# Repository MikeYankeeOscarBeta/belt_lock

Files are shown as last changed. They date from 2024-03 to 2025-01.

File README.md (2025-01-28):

# belt_lock
by [MikeYankeeOscarBeta](https://github.com/MikeYankeeOscarBeta/) (VoronDesign Discord: #MikeyMike V2.5796, Voron Toolchangers Discord: MikeyMike - Github: [MikeYankeeOscarBeta](https://github.com/MikeYankeeOscarBeta/StealthChanger))

## Description
A solution for mounting 9mm and 6mm 2mgt/2gt GT2/GT3 belts to mgn12 carriage with M2-SHCS or 2mm pin. Designed to handle high belt tensions.
Versions for both inverted and normal belts.

## Features
- Belt Pin
- Does not clamp the belt against the carriage, carriage-wipers or anything other than itself
- For monolith (inverted belts) it will not change the belt path (keeps the belt path perfectly straight)
- For normal belt direction there will be a ~0.8mm y offset
- Keeps within the confines of the carriage (unless using the external clamps)
- builds just 6mm out in y
- Tested with 15kg static load per belt

## BOM
| Part | Amount | Description |
|---|---|---|
| M2x25mm SHCS or 2x25mm PIN  | 4 |  Pin leaves more material, hence stronger. |
| | |  M2 SHCS for ease of use |
| | |  (only 2 screws if using single pin and clamp version (shuttle_clamper_body_v75) |

## Print Instructions
- Print it upright, the strength comes from the layer direction. printing it in the incorrect orientation will result in a weaker part.  
- Use support (make sure your supports are tuned to the point where you're able to remove them carefully without breaking the part).  
- 40%+ infill  
- 4 perimitters  
- 4 top and bottom layers  
- 0.2mm layer height  (or smaller)
- 0.4mm nozzle (or smaller)
- enable filling gaps

## Part Instructions
### shuttle_clamper_body_v101_inverted_belt_gt2_epdm
main body, for no loss in x.
For inverted belts in EPDM (LL-GT2 E) and GT3. will be too loose for normal GT2 (rubber) belts.
Should work with GT2 RF (rubber/normal) belts as well, but will slip sooner (<15kg)

### shuttle_clamper_body_v96_*
main body, for no loss in x.
For inverted belts gt2 rubber belts (LL-2GT RF). Too tight for GT2 EPDM or GT3.

### shuttle_clamper_body_v96_normal_belt
For normal (non-inverted) GT2-R (rubber) belts.

### shuttle_clamper_body_v75
Single pin, no teardrop lock. For both normal and inverted belts. GT2 rubber and epdm, and GT3.
Requires use with a clamp like m2_belt_clamp or m3_BeefyBeltClamp.

### m2_belt_clamp
small footprint belt clamp using m2 screws and heatset nuts.

### m3_BeefyBeltClamp
Beefy clamp using m3 screws and hexnuts.

### BOM - m2_belt_clamp
| Part | Amount | Description |
|---|---|---|
| m2x4x3.5 Heatset Nut | 6 |  4mm deep, m2 threads, 3.5mm outer diameter |
| m2x10mm SHCS Screw | 6 |  m2x12 SHCS also works ok |

### BOM - m3_BeefyBeltClamp
| Part | Amount | Description |
|---|---|---|
| m3 hexnut | 6 | |
| m3x8mm SHCS Screw | 6 | m3x12 SHCS also works |

## Support
Raise issues via github or contact via discord.
Voron Toolchangers Discord "Belt Lock" thread: https://discord.com/channels/1119433664799965186/1218280403870289990

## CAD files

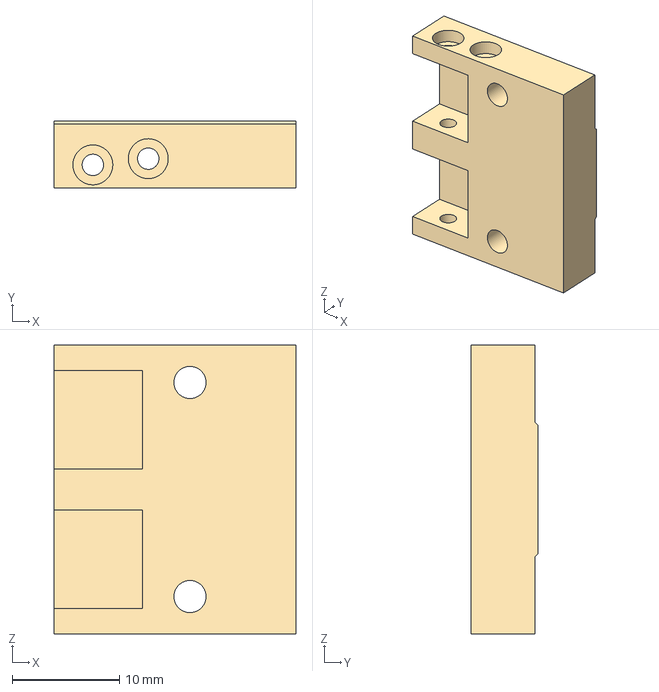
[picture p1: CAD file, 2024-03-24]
CAD/shuttlething_v0.3_v101_inverted_belt_gt2_epdm.step
22.6 x 6.30 x 27.0 mm

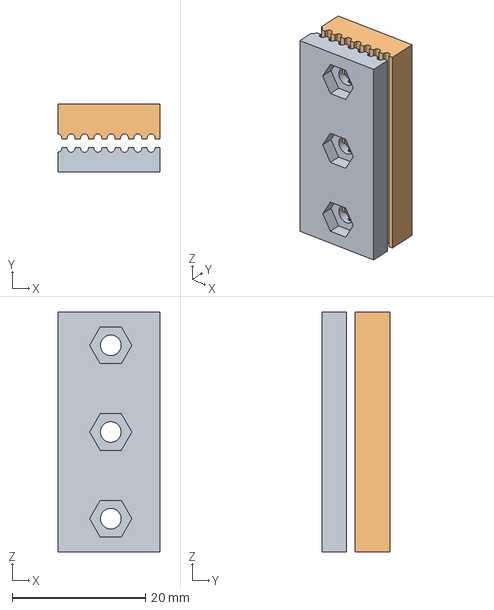
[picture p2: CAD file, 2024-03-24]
CAD/m3_BeefyBeltClamp_v2.step
15.3 x 10.2 x 36.0 mm

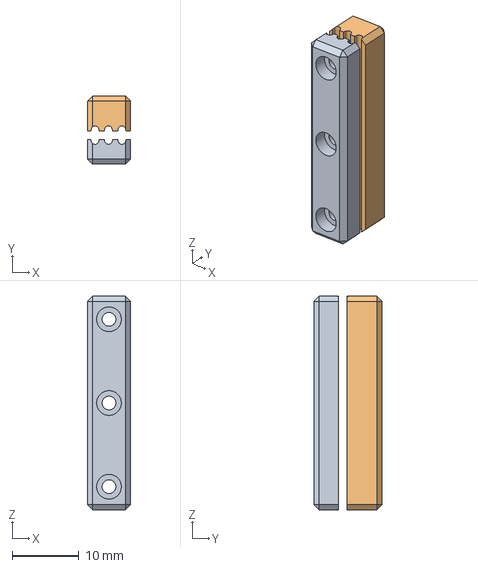
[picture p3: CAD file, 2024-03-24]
CAD/m2_belt_clamp_v70.step
6.50 x 10.2 x 32.0 mm
m2_belt_clamp_a
m2_belt_clamp_b

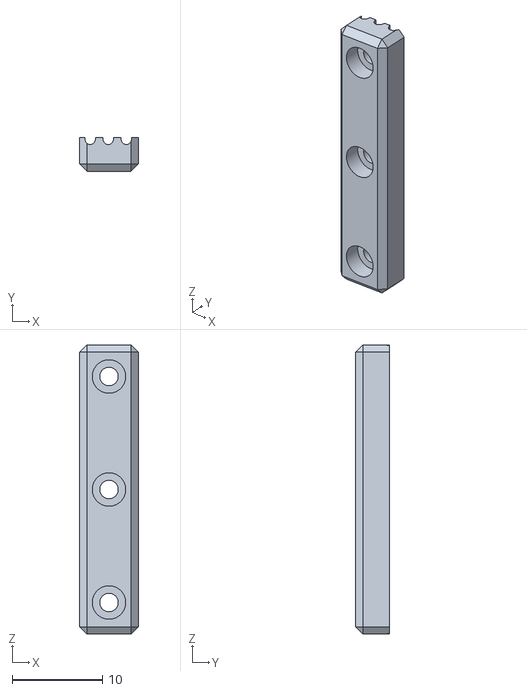
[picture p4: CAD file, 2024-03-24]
STL/m2_belt_clamp_a_v70.stl
6.50 x 3.71 x 32.0

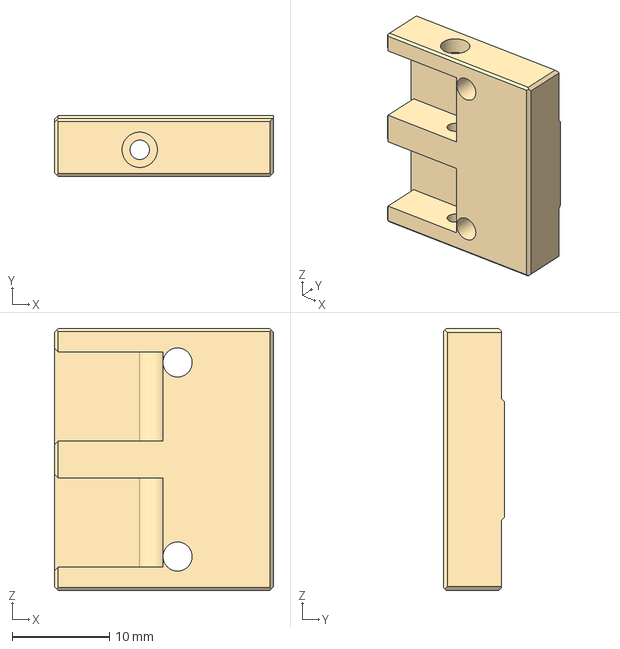
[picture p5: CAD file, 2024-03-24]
CAD/shuttle_clamper_body_v75.step
22.6 x 6.30 x 27.0 mm

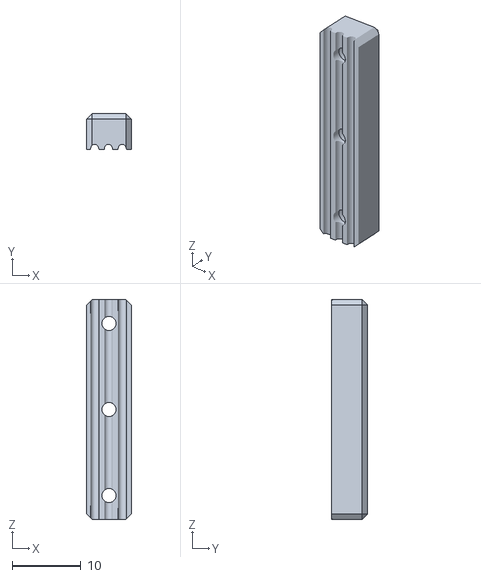
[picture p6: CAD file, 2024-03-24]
STL/m2_belt_clamp_b_v70.stl
6.50 x 5.24 x 32.0

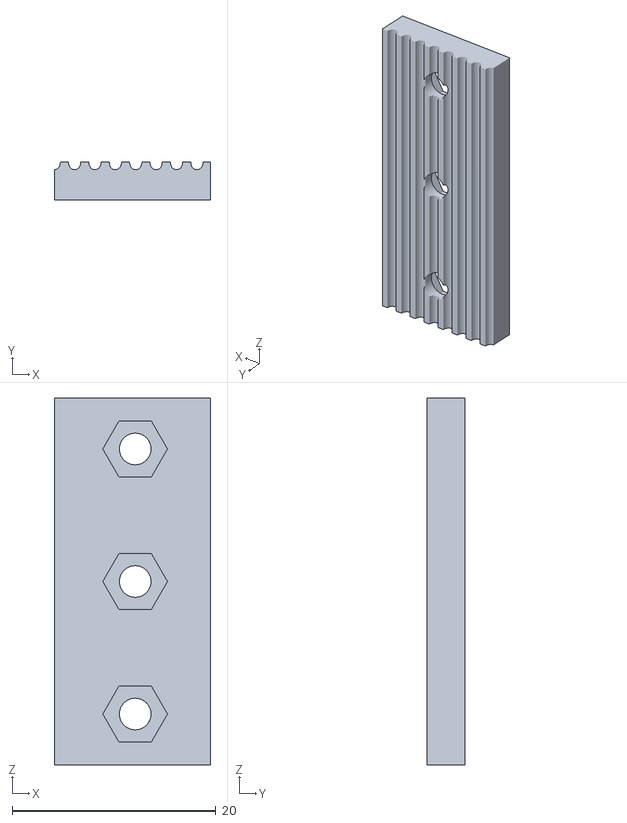
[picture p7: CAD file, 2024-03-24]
STL/m3_BeefyBeltClamp_a_v2.stl
15.3 x 3.71 x 36.0

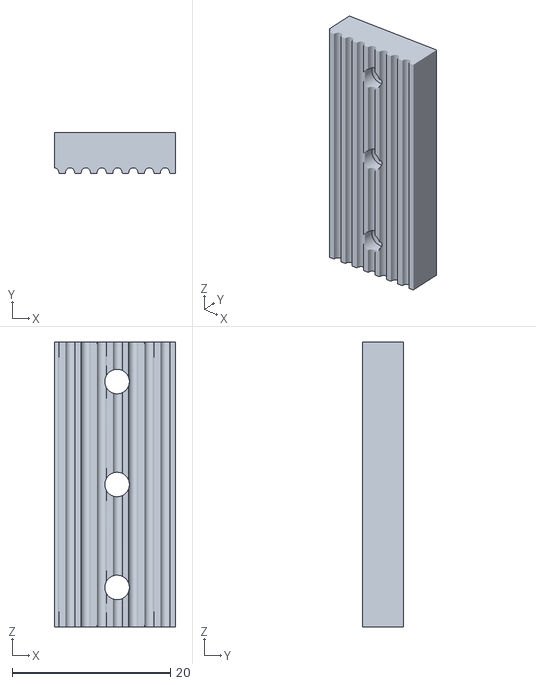
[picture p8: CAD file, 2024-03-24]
STL/m3_BeefyBeltClamp_b_v2.stl
15.3 x 5.24 x 36.0

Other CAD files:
STL/shuttle_clamper_body_v101_inverted_belt_gt2_epdm.stl
STL/shuttle_clamper_body_v96_normal_belt.stl
CAD/shuttlething_v0.3_v96_2mm_pin_inverted_belt.step
STL/shuttle_clamper_body_v96_inverted_belt.stl
CAD/shuttlething_v0.3_v96_inverted_belt.step
STL/shuttle_clamper_body_v96_2mm_pin_inverted_belt.stl
CAD/shuttlething_v0.3_v96_normal_belt.step
CAD/shuttlething_v0.3_2mm_pin_normal_belt.step
STL/shuttle_clamper_body_2mm_pin_normal_belt.stl
STL/shuttle_clamper_body_v75.stl

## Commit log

2024-03-24 initial commit
    add readmy, stl and step files.
    [m2_belt_clamp_a_v70.stl, m2_belt_clamp_b_v70.stl, m2_belt_clamp_v70.step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]
2024-03-24 add bom
    add bom
2024-03-24 add gt2 epdm and gt3 versions
    [shuttle_clamper_body_v101_inverted_belt_gt2_epdm.stl, shuttlething_v0.3_v101_inverted_belt_gt2_epdm.step]
2024-03-24 add belt_lock f3d
2024-03-24 Update belt_lock_export_202403242304 v2.f3d
